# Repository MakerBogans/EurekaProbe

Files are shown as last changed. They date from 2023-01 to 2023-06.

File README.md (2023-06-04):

# EurekaProbe

top

The EurekaProbe is a PCB based microswitch probe for 3D printers. This project takes inspiration from [Klicky](https://github.com/jlas1/Klicky-Probe/), [Euclid](https://github.com/nionio6915/Euclid_Probe) and [QuickDraw](https://github.com/Annex-Engineering/Quickdraw_Probe).

The aim of this project is to synthesise some of the best ideas from those other projects and distill them into a highly reliable, simple, robust, cost effective and easy to source alternative.

EurekaProbe is initially developed to be paired with the [DirtyBird](https://github.com/MakerBogans/dirtybird) toolhead for Voron CoreXY printers, however can be adapted to to all other toolheads (AfterBurner, StealthBurner, etc).

Construction of EurekaProbe uses two identical PCBs which are magnetically coupled with countersunk 8x3 magnents. The PCBs are reversible, with one soldered as the Probe PCB and the other is attached onto the toolhead.

Operation of the probe uses Klicky based macros to ensure the probe correctly attaches from the dock before probing the bed.

## But what's the point/benefit of this over existing probes?

- PCB based design ensures the magnets are always secured and correctly seated. No glues required, no ongoing maintenance, always repeatable coupling
- Unlike Euclid which has a voltage input and rating due to the LED circuit, Eureka does away with any voltage in the circuit because it is just a microswitch like any other endstop. So there is virtually no chance of backfeeding 24V or similar back to your MCU. All you need is to connect it to signal and ground on a endstop port
- Cheaper, easier to source than Euclid (at least for us Aussies), with a more generous licence arrangement

## Acknowledgements
Thank you to the [MakerBogans](https://github.com/MakerBogans) for supporting and assisting with development of this project.

## BOM
- 2	* EurekaProbe PCB [JLCPCB](https://jlcpcb.com/)
- 4	* 8x3-3 Countersunk magnets [Aliexpress](https://www.aliexpress.com/item/1005001610172466.html)
- 4 * M2.5x5mm Torx countersunk screw [Aliexpress](https://www.aliexpress.com/item/33006942612.html)
- 4 * SMTSO-M2.5-2.5ET [Aliexpress](https://www.aliexpress.com/item/1005003780036815.html)
- 2 * M3x5mm low profile bolt [Aliexpress](https://www.aliexpress.com/item/33049052926.html)
- 2 * M3x5x4 heat inserts [Aliexpress](https://www.aliexpress.com/item/1005003314830904.html)
- 1 * Omron D2F [DigiKey](https://www.digikey.com.au/en/products/detail/omron-electronics-inc-emc-div/D2F-5/8593136)
- 1 * JST B2B-XH-A [Aliexpress](https://www.aliexpress.com/item/4000029861567.html)

## Purchasing a Eureka Probe kit

- [Orvil3D (AU)](https://orvil3d.com/products/eureka-probe)

## Assembly

eurekacarriage

- Solder SMTSO nuts to both PCBs
- Solder microswitch to one of the PCBs (The middle pin of the microswitch is not connected to the circuit on the PCB so it is safe to solder to the PCB to ensure a stronger bond between the microswitch and the PCB)
- Solder JST header to the other PCB
- Screw countersunk magents to PCBs via SMTSO nuts with Torx screws. Ensure you have mixed polarity across the pairs
- Attach toolhead PCB to carriage via M3x5 low profile bolts into heat inserts

## Carriage mounts

A Eureka compatible carriage is avilable for the DirtyBird toolhead over on [the projects GitHub Page](https://github.com/MakerBogans/dirtybird/blob/main/3mf/Carriage/DB_Eureka_Carriage_JST.3mf)

## Probe docks

A dock is available Voron Trident and Voron V2. It is compatible with Klicky style mounts and includes a fixed sidemount designed to suit the Voron Trident/V2 with a Dirtybird toolhead carriage. Other printers are likely to work with the variable Klicky arm but are untested.

### Voron Trident and Voron 2.4 probe dock

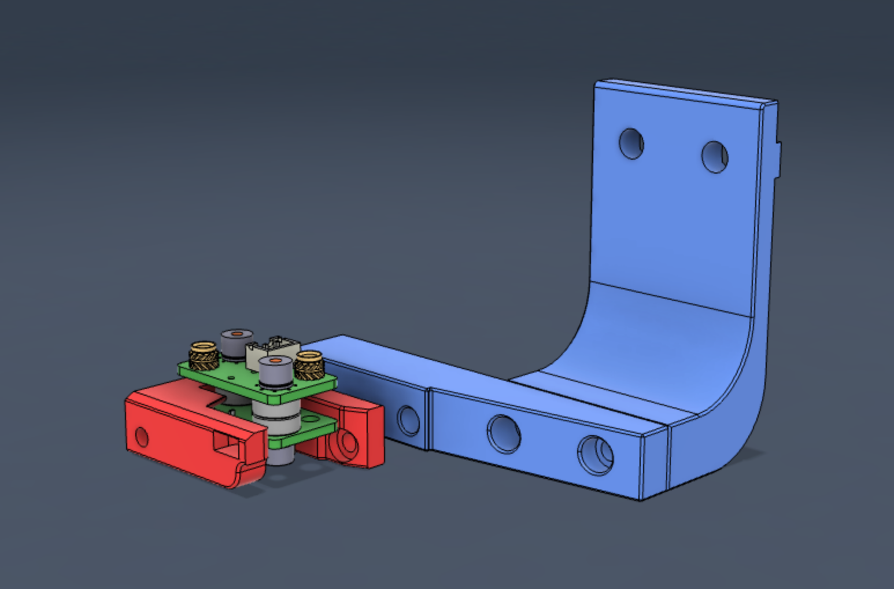
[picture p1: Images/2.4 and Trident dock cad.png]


Printed parts are pre-oriented for printing. Use your typical Voron part settings to print.

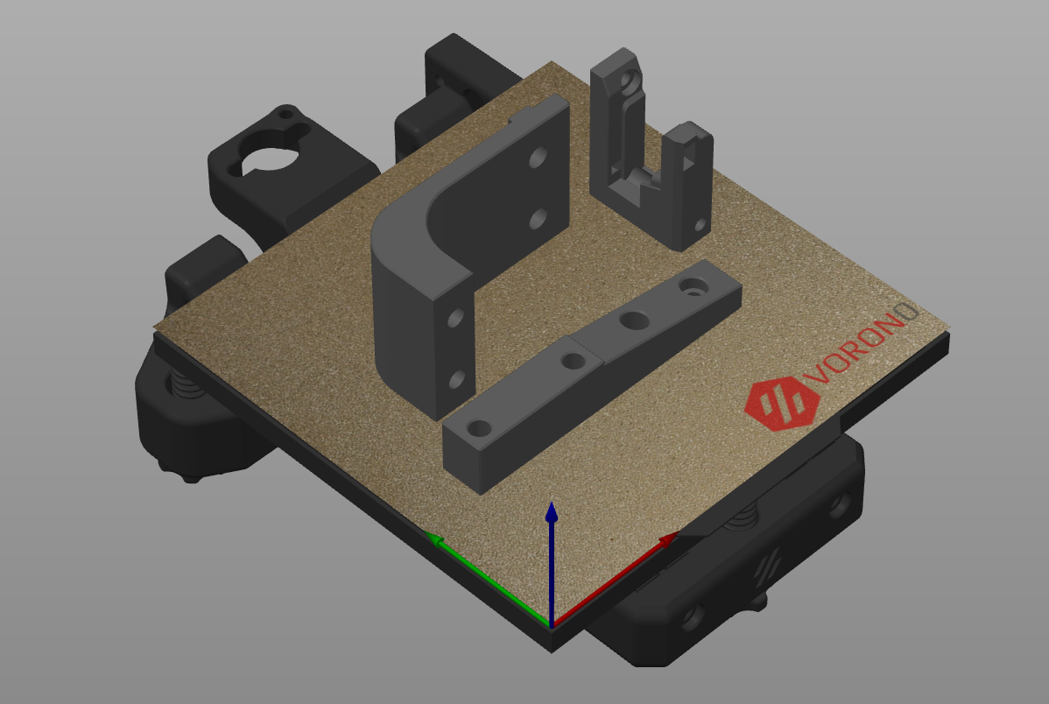
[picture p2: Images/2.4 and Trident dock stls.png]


- 1 x [Eureka Voron Dock](STLs/Eureka%20Dock.stl)
- 1 x [Eureka Voron Dock Arm](STLs/Eureka%202.4%20and%20Trident%20Dock%20Arm.stl)
- 1 x [Eureka Voron Dock Sidearm](STLs/Eureka%202.4%20and%20Trident%20Dock%20Sidearm.stl)

**BOM**

- 4 * M3x8mm SHCS
- 4 * M3x5x4mm heat inserts [Aliexpress](https://www.aliexpress.com/item/1005003314830904.html)
- 2 * M5x10mm BHCS
- 2 * M5 T-Nuts for 2020 extrusion
- 2 * 6mmx3mm round magnets

**Assembly**

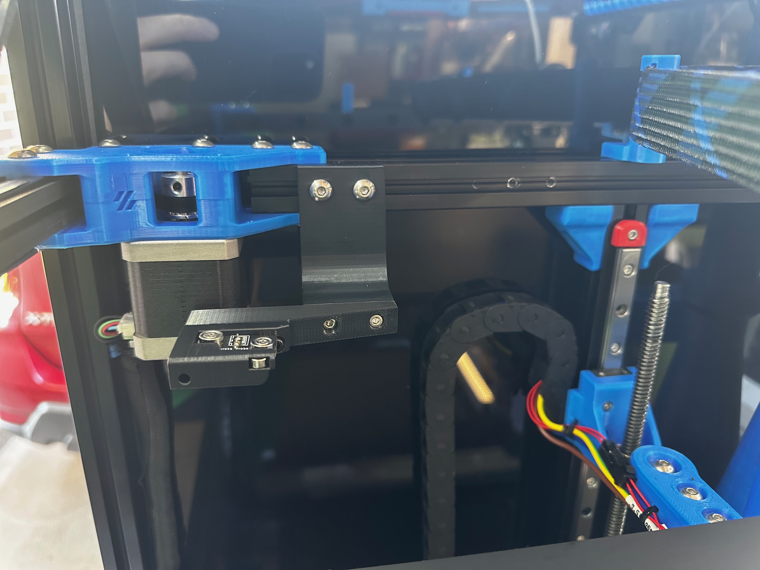
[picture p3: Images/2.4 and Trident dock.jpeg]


- Fit heat inserts into the dock arm and dock sidearm
- Screw the sidearm to the gantry arm using 2 x M3x8
- Fit 6x3 magnets into the side of the dock. It is normal for it to crack the top plastic slightly. If it has made the dock prone to breaking then the dock may need to be printed with a lower extrusion multiplier to allow more room for the magnets
- Screw the dock to the to the side arm using 2 x M3x8
- Insert the two t-nuts into the gantry extrusion
- Screw the dock to the gantry using 2 x M5x10

**Example klick configuration**

The Trident dock is designed to dock and undock the probe at the real left max units of the printer. On a Trident 250 this would be `X,Y = 0,250`. You are free to position the dock anywhere you like, this is what works for me.

Main `klicky-variables.cfg` changes required to get up and running.

```ini
# Set to 0 to have the probe move to center of bed
variable_z_endstop_x: 0
variable_z_endstop_y: 0

# Dock location
variable_docklocation_x:   0 # X Dock position
variable_docklocation_y: 250 # Y Dock position

# Dock move.
# Final toolhead movement to release the probe on the dock.
# Values are a relative move.
Variable_dockmove_x:   0
Variable_dockmove_y: -40
Variable_dockmove_z:   0

# Attach move.
# Final toolhead movement to attach the probe on the mount.
# Values are a relative move.
Variable_attachmove_x: -50
Variable_attachmove_y:   0
Variable_attachmove_z:   0

# Back off from Y endstop when homing to avoid accidentality
# docking the probe.
variable_home_backoff_y: 40
```

*Remember*: these values are a guide only. Follow the [Klicky-macros](https://github.com/jlas1/Klicky-Probe/tree/main/Klipper_macros) documentation when setting up the dock location for the first time.

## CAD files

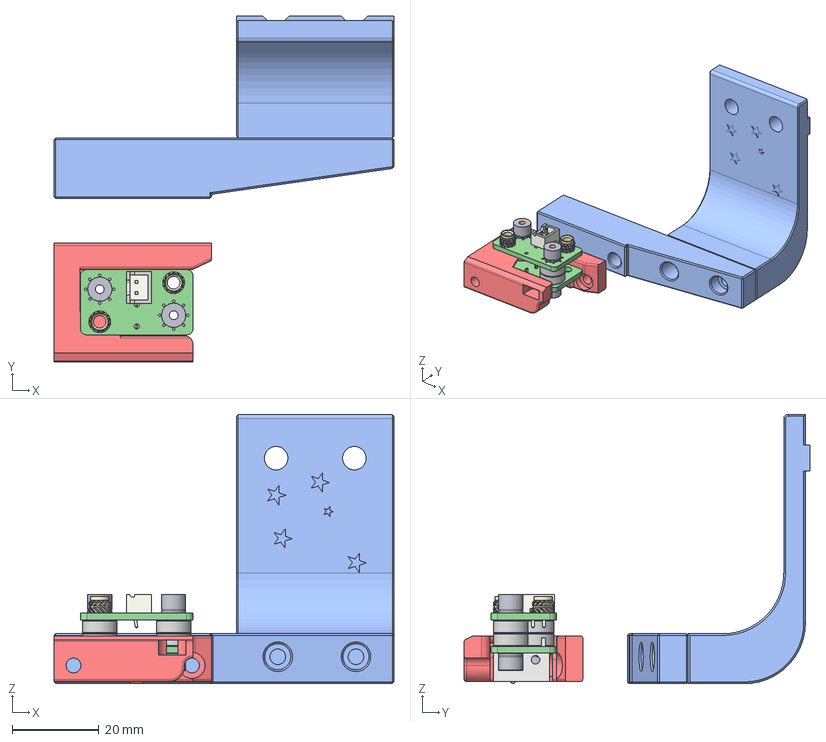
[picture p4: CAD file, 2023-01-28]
CAD/Eureka Probe Mount.step
78.3 x 79.6 x 62.0 mm
SMTSO-2.5-5ET
SMTSO-2.5-5ET (1)
PCB (1)
Magnets8x3-3 (1)
M3 Threaded Insert v1 (2) (1) (2) (1)
M3 Threaded Insert v1 (2) (1) (2) (1) (1)
SMTSO-2.5-4ET (1)
SMTSO-2.5-4ET
PCB
Magnets8x3-3
D2F_L_BASE (1) (3)
Probe Dock
Probe Sidemount

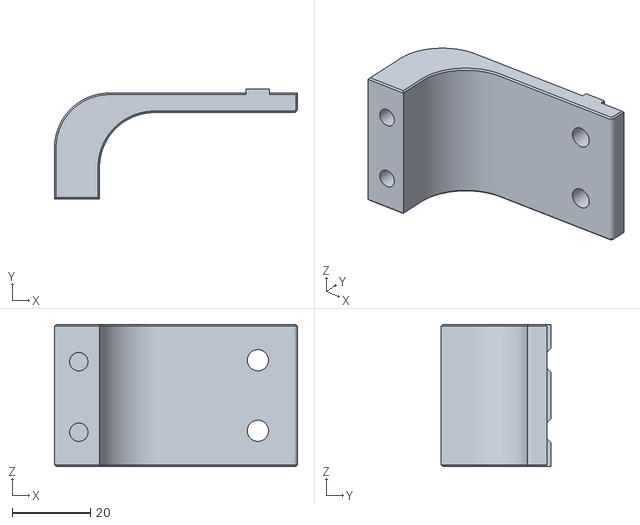
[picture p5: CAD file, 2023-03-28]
STLs/Eureka 2.4 and Trident Dock Arm.stl
62.0 x 28.0 x 36.3

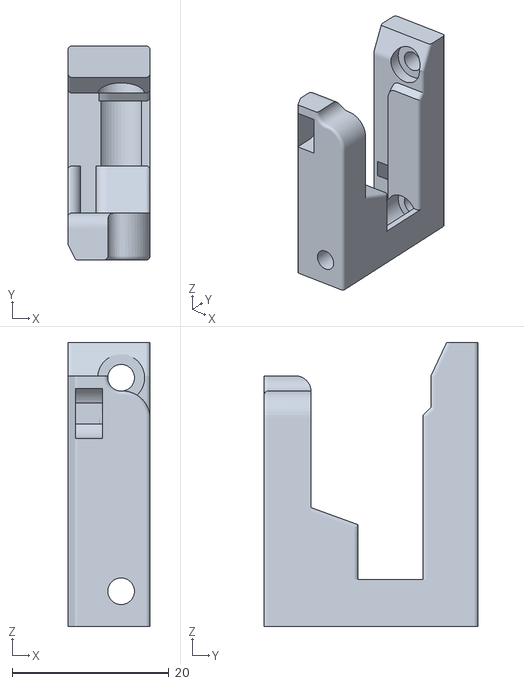
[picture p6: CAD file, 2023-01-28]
STLs/Eureka Dock.stl
10.5 x 27.3 x 36.3

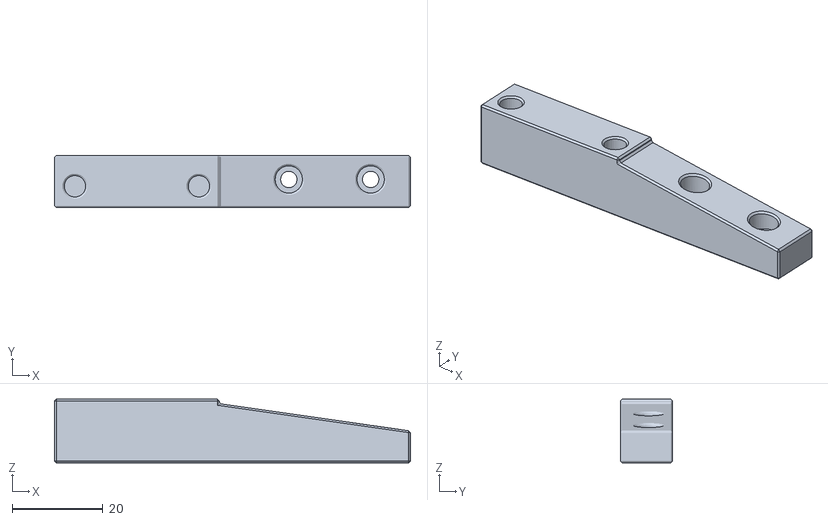
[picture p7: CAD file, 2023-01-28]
STLs/Eureka 2.4 and Trident Dock Sidearm.stl
78.3 x 11.5 x 14.0

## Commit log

2023-01-28 Add initial Trident probe dock
    [Eureka Dock.stl, Eureka Probe Mount.step, Eureka Trident Dock Arm.stl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]
2023-01-28 Gerber files
    [EurekaProbe0.0.2-B_Cu.gbr, EurekaProbe0.0.2-B_Mask.gbr, EurekaProbe0.0.2-B_Paste.gbr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]
2023-03-28 Update to reference Voron 2.4 along with Trident in dock support
    [Eureka 2.4 and Trident Dock Arm.stl, Eureka 2.4 and Trident Dock Sidearm.stl, Eureka Trident Dock Arm.stl]
